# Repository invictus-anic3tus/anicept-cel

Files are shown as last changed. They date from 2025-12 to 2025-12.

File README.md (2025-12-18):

<div align="center">
  Anicept Cel Title Image

  <h2>By Anicetus</h2>

  <p display="inline">
  
  <a href="https://creativecommons.org/licenses/by-nc/4.0/">
    </a> <a href="https://hackclub.com/highway">
    
  </a>

  </p>

  <h4>A tiny yet mighty, sturdy and swift 3D printer, designed and optimized to run at tremendous speeds.</h4>
</div>

<sub>This work is licensed under a
[Creative Commons Attribution-NonCommercial 4.0 International License](https://creativecommons.org/licenses/by-nc/4.0/).
</sub>

## Table of Contents

- [About](#about)
- [Features and Specifications](#features-and-specifications)
- [Assembly](#assembly)
- [Bill of Materials](#bill-of-materials)
- [Contributing](#contributing)

# About

Well, here we go again. My name is Anicetus, and this is my second 3D printer design to date. The first flopped miserably, due to numerous issues in the design phase that either I overlooked or missed due to a lack of research.

Not this time.

This time, I'm making a _real_ printer. Not just another mid ender 3 clone, this is (or should be; as I'm writing this I haven't built it lol) something special. But let's start with the name, shall we? It's called the Anicept Cel. The first part is easy enough to explain--any dedicated hardware enthusiast should have a brand name. Anicept is a combination of Anicetus and concept, and I like how it feels. As for Cel, it's my newfound custom to name my printers with three-letter words. I took Cel from the Latin word celer, or "fast". Maybe that tells you a bit about what I was going for here.

That's right, this printer is made for speed. Everything about it, from the head to the feet (ha) was specifically bent on pure speed. Of course, I'm not an infinite money generator, so I had limits. But not _that_ many limits.

# Features and Specifications

- 180 x 180 x 160 mm print size, plenty for almost all applications
- 300°C max printing temp
- Uses the Peopoly Lancer Long Melt Zone hotend, capable of up to 60mm<sup>3</sup>/s flow rate
- Powerful sheet cooling, best for PETG and ABS/ASA, with the use of two 5020 part cooling fans
- Uses the CR-Touch, one of the most precise (and expensive lol) ABL probes available
- All-4040 extrusion frame, increasing sturdiness exponentially
- MGN12H rails all-around, minimizing wobble
- AWD (all wheel drive) on both Y and X axes, exponentially increasing its power
- Belted Z axis
- Separate electronics enclosure, for ease of use/assembly and to allow enclosing the main printer
- Extra 48V PSU for motors only, increasing their torque
- 9mm belt on X and Y axes
- Uses the powerful Octopus Pro mainboard, equipped with TMC5160T Pros for the X and Y axes
- Uses the Protoextruder, an open-source, DIY filament extruder
- Compatible with the Pico MMU and filament cutter, enabling 4-color and multimaterial printing

# Assembly

coming soon...

# Bill of Materials

Very WIP!! Also this is my personal BOM, like what I own and don't own. Aliexpress prices subject to change _violently_.

|Item |Link |Alt link |Cost |Quantity|Extended Cost|Notes |
|---|---|---|---|---|---|---|
|Electronics |$172.85 | | | | | |
|24V 600W PSU |https://www.digikey.com/en/products/detail/mean-well-usa-inc/LRS-600-24/16394242 | |$70.00 |1 |$0.00 |Owned |
|48V 480W PSU |https://www.amazon.com/REALSUN-Universal-Switching-Converter-Transformer/dp/B096VJMQFM/| |$26.99 |1 |$26.99 | |
|BigTreeTech Octopus Pro + TMC5160T Pro x 4|https://www.aliexpress.us/item/3256803375036597.html | |$100.26|1 |$100.26 | |
|TMC2209 |https://www.aliexpress.us/item/3256805074646808.html | |$0.99  |4 |$3.96 | |
|24v 4010 Axial Fan |https://www.aliexpress.us/item/3256803185681643.html | |$0.99  |1 |$0.99 |(2 pcs needed, 1 owned) |
|RPi 4B 1GB RAM |https://www.ebay.com/itm/167900769294 | |$24.99 |1 |$24.99 | |
|Power inlet |https://www.aliexpress.us/item/3256806175041706.html | |$1.53  |1 |$0.00 |Owned |
|Power cord |https://www.aliexpress.us/item/3256802936747637.html | |$2.61  |1 |$0.00 |Owned |
|On button |https://www.adafruit.com/product/481 | |$4.95  |1 |$0.00 |Owned |
|Heated bed |https://www.aliexpress.us/item/3256807101964868.html | |$14.67 |1 |$14.67 |2M cable? |
|1M 13mm Wire sleeve |https://www.aliexpress.us/item/3256802043851957.html | |$0.99  |1 |$0.99 | |
|Zip ties | | |$2.00  |1 |$0.00 |Owned |
|12AWG Wire |https://www.aliexpress.us/item/3256806250298216.html | |$0.99  |1 |$0.99 |2 M - 1m red, 1m black |
|12AWG Fork Connectors (18 min) |https://www.aliexpress.us/item/3256805357612913.html | |$0.99  |1 |$0.99 |8mm outer width, >= 4mm ID |
|12AWG Female Fork Connectors | | |$0.99  |3 |$0.00 |Owned |
|Frame |$91.47 | | | | | |
|4040 x 600mm extrusion (4 pack) |https://www.amazon.com/gp/product/B09MYL6XMY/ | |$62.99 |1 |$62.99 |Self-cut |
|2020 x 250mm extrusion |https://www.aliexpress.us/item/3256803124984194.html |https://www.aliexpress.us/item/3256804493383834.html|$7.10  |1 |$7.10 | |
|T Plates |https://www.aliexpress.us/item/3256806516993865.html |https://www.aliexpress.us/item/3256806574844240.html|$7.91  |1 |$7.91 | |
|Bed plate |https://www.aliexpress.us/item/3256802956143480.html | |$12.48 |1 |$12.48 | |
|M5 Tap |https://www.aliexpress.us/item/3256805979008585.html | |$0.99  |1 |$0.99 | |
|Tap Wrench |https://www.aliexpress.us/item/3256808061844390.html | |$0.99  |1 |$0.99 | |
|Motion |$41.74 | | | | | |
|X/Y Motors |https://www.aliexpress.us/item/2255801033887365.html | |$22.55 |1 |$0.00 |Owned |
|MGN12H x 250 |https://www.aliexpress.us/item/2255800576028509.html | |$9.05  |3 |$27.15 |(owned: 2, total qty: 5) |
|9mm 2GT Belt |https://www.aliexpress.us/item/3256806321466333.html | |$13.35 |1 |$0.00 |Owned |
|16T 10W 5B Pulley (5 pcs) |https://www.aliexpress.us/item/2251832595367020.html | |$0.99  |1 |$0.99 | |
|20T 10W 5B Pulley | | | |2 |$0.00 |Y axis, owned |
|605 (5x14x5) Bearing (10pcs) |https://www.aliexpress.us/item/3256807482131308.html | |$0.99  |1 |$0.99 |4 Owned, 10 to buy |
|Z axis | | | | | | |
|Motors |https://www.aliexpress.us/item/3256808273084374.html | |$2.46  |2 |$4.92 | |
|80T - 20T pulley, 200mm belt reduction kit|https://www.aliexpress.us/item/3256808844764521.html | |$1.37  |2 |$2.74 | |
|20T 6W 5B Pulley |https://www.aliexpress.us/item/3256806031359840.html | |$0.99  |1 |$0.99 |(owned: 1, total qty: 2) |
|20T 6W 5B Idler |https://www.aliexpress.us/item/2251832631013486.html | |$0.99  |2 |$1.98 | |
|6mm 2GT belt (2M) |https://www.aliexpress.us/item/3256806321466333.html | |$0.99  |1 |$0.99 | |
|M5x45 Dowel pin |https://www.aliexpress.us/item/3256806837028480.html | |$0.99  |1 |$0.99 |(6 pcs min, self cut) |
|Printhead |$85.45 | | | | | |
|Orbiter V2.0/V2.5 |https://www.aliexpress.us/item/3256807258760130.html | |$34.28 |1 |$0.00 |Owned |
|Peopoly Lancer Long Melt Zone |https://peopoly.net/products/magneto-x-lancer-melt-zone | |$58.00 |1 |$58.00 | |
|5020 Fan (2pcs) |https://www.aliexpress.us/item/3256807407728580.html | |$9.53  |1 |$9.53 | |
|CR Touch |https://www.aliexpress.us/item/3256806043295649.html | |$14.95 |1 |$14.95 | |
|Microswitch (3pcs; 2pcs used for X+Y axes)|https://www.aliexpress.us/item/3256804568049753.html | |$0.99  |1 |$0.99 | |
|ADXL345 |https://www.aliexpress.us/item/3256806996565152.html | |$2.33  |1 |$0.00 |Owned |
|3010 Heat Sink Cooling Fan |https://www.aliexpress.us/item/3256803185681643.html | |$0.99  |1 |$0.00 |Owned |
|Filament Cutter + Sensor | | | | | | |
|4mm OD 2mm ID PTFE Tube |https://www.aliexpress.us/item/3256806056618135.html | |$2.01  |1 |$0.00 |Owned |
|Exacto Knife #11 Blade |https://www.aliexpress.us/item/3256808331067380.html | |$0.99  |1 |$0.99 | |
|4mm Ball Bearing |https://www.aliexpress.us/item/3256803905354831.html | |$0.99  |1 |$0.99 | |
|Fasteners and Miscellaneous |$16.10 | | | | |EXACT SCREW NEEDS ARE WIP! |
|Nozzle wiper |https://www.aliexpress.us/item/3256807315758369.html | |$0.99  |1 |$0.99 | |
|M3x22 SHCS | | | |4 |$0.00 |Owned |
|M3x30 SHCS | | | |4 |$0.00 |Owned |
|M3x8 SHCS | | | |7 |$0.00 |Owned |
|M3x6 SHCS | | |$0.99  |1 |$0.99 |for the electronics box |
|M3x14 SHCS | | | |12 |$0.00 |Owned |
|M4x12 FHCS | | | |6 |$0.00 |for the bed & X axis tensioner (owned)|
|M5x50 SHCS |https://www.aliexpress.us/item/2255800598515019.html | | |40 |$3.96 | |
|M5x14 SHCS |https://www.aliexpress.us/item/2255800598515019.html | | |10 |$0.99 |(Total 22, owned 12) |
|2020 M3 T Nuts (50 pcs) |https://www.aliexpress.us/item/3256807638725964.html | | |1 |$0.99 | |
|2020 M5 T Nuts (50 pcs) |https://www.aliexpress.us/item/2251832778465720.html | | |1 |$0.99 | |
|M5 Two-Stage Drill Bit |https://www.aliexpress.us/item/3256805825438819.html | |$6.20  |1 |$6.20 | |
|M3x4mm 5mm OD inserts |https://www.aliexpress.us/item/3256803396040989.html | |$0.99  |1 |$0.99 | |
|M4x8mm 6mm OD inserts | | | | |$0.00 |Owned |
|M5x8mm 7mm OD inserts |https://www.aliexpress.us/item/3256803396040989.html | |$0.99  |1 |$0.99 | |
|Total | | | | |$411.57 | |
|Tax | | | | |$33.95 | |
|Grand Total | | | | |$445.52 | |

# Contributing

If you'd like to request something, give feedback, or wish to make your own changes, simply open an issue on this repository or email me! (My email is in my profile.)



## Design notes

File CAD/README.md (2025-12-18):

Hi there! Herein lies the complete (WIP!) files for the Anicept Cel and its electronics box. In the 3D_Print directory, you'll find all the files you need to 3D print, categorized as seen fit.













thats it. go away

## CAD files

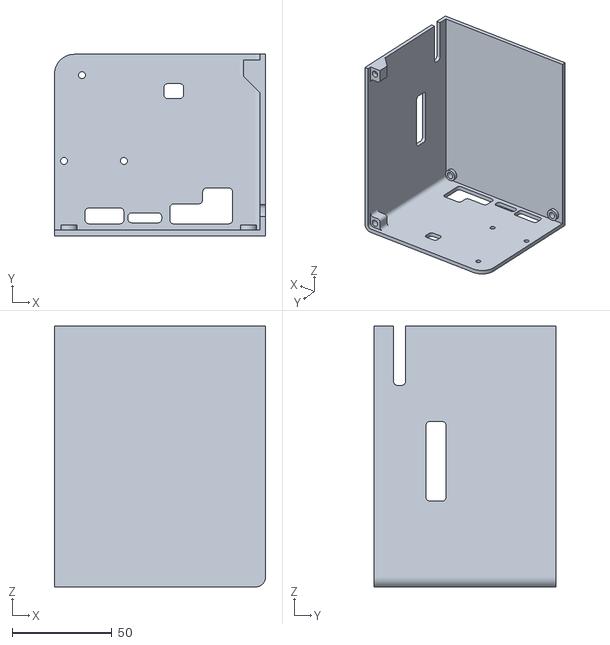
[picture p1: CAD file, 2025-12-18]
CAD/3D_Print/Electronics_Box/Main Casing 2.stl
105.8 x 91.0 x 130.8

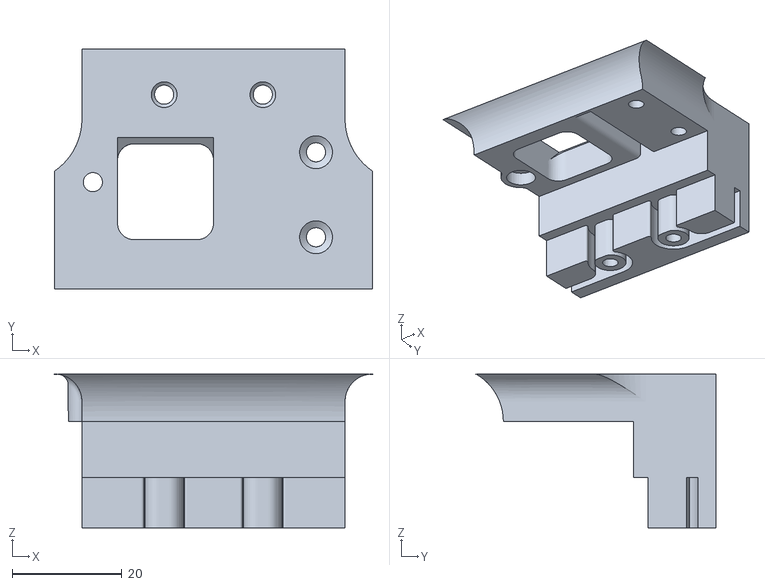
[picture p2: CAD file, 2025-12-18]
CAD/3D_Print/Main_Printer/Printhead/Printhead Back Main.stl
58.0 x 43.8 x 28.1

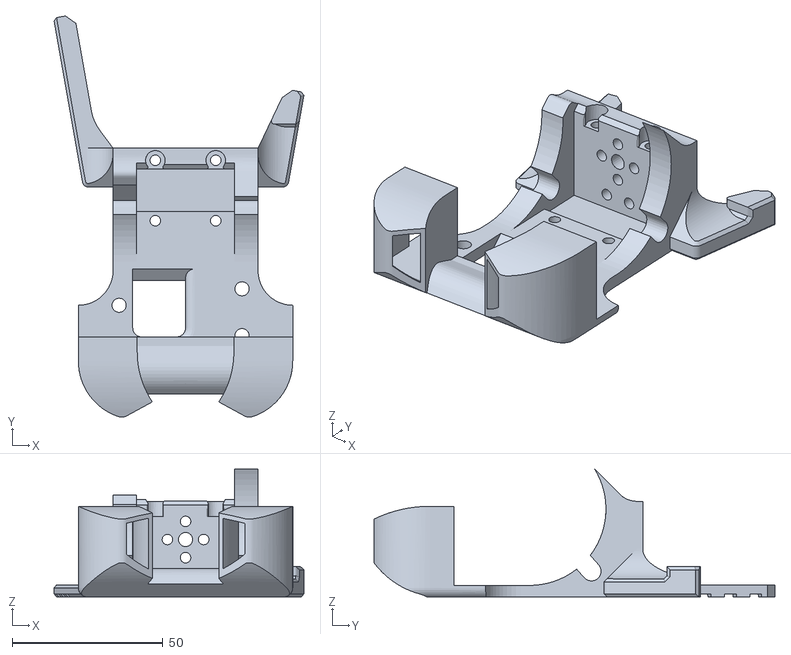
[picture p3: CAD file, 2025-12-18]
CAD/3D_Print/Main_Printer/Printhead/Printhead Main.stl
82.7 x 132.8 x 42.4

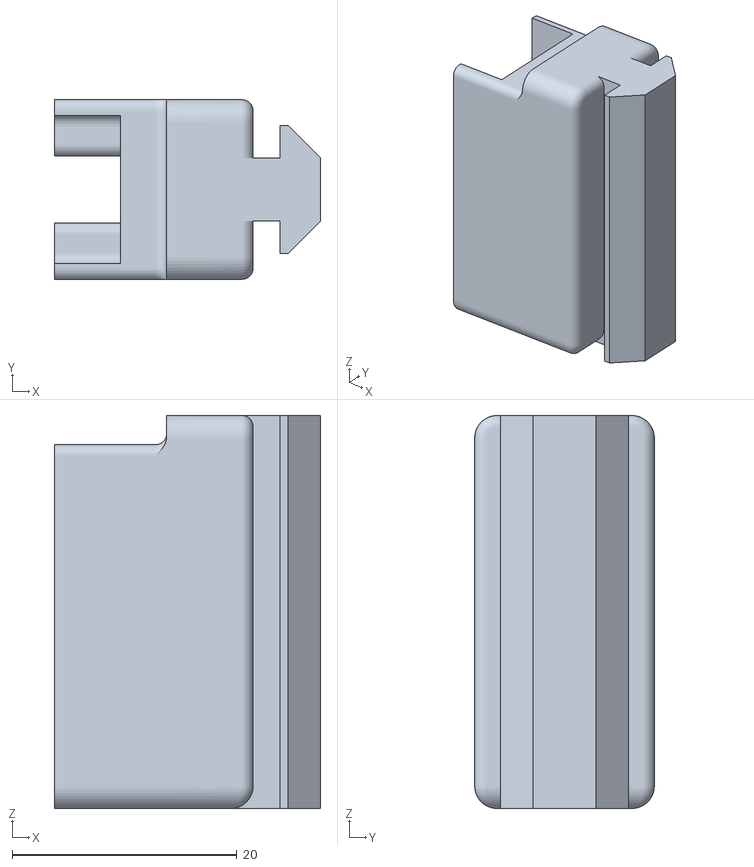
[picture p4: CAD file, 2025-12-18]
CAD/3D_Print/Main_Printer/Y_Axis/Y Axis Endstop Main.stl
23.7 x 16.0 x 35.0

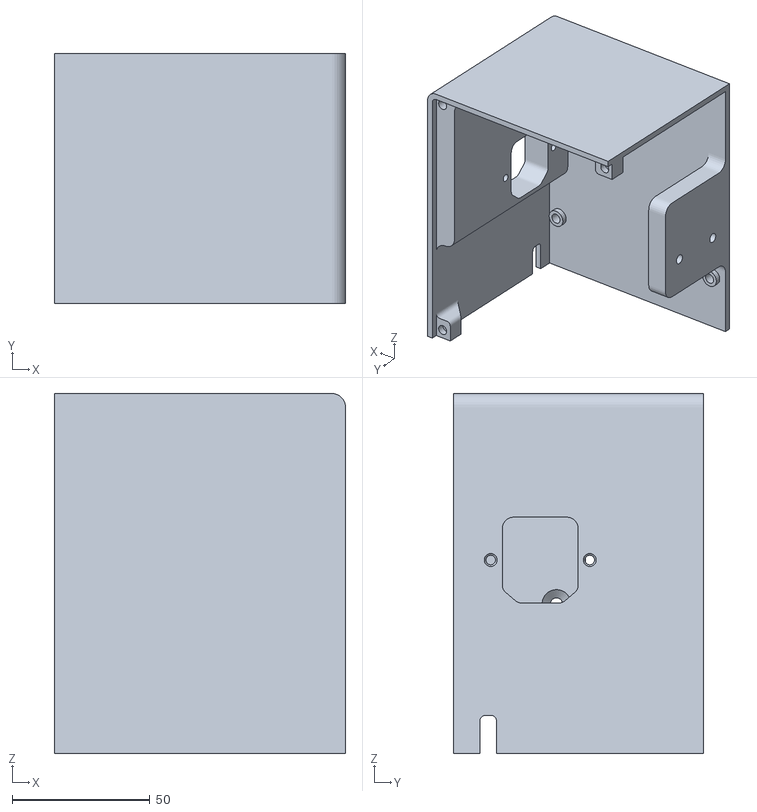
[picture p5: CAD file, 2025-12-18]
CAD/3D_Print/Electronics_Box/Main Casing 1.stl
105.8 x 91.0 x 130.8

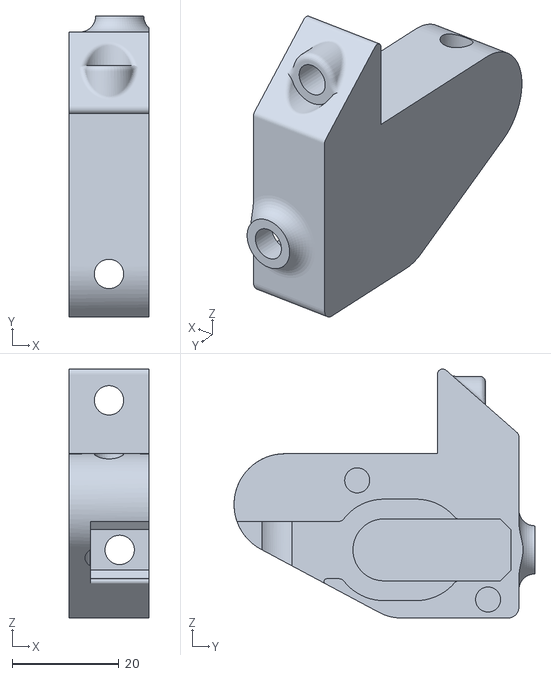
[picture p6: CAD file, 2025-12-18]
CAD/3D_Print/Main_Printer/Z_Axis/Z Axis Left Belt Tensioner Main.stl
15.0 x 56.3 x 46.6

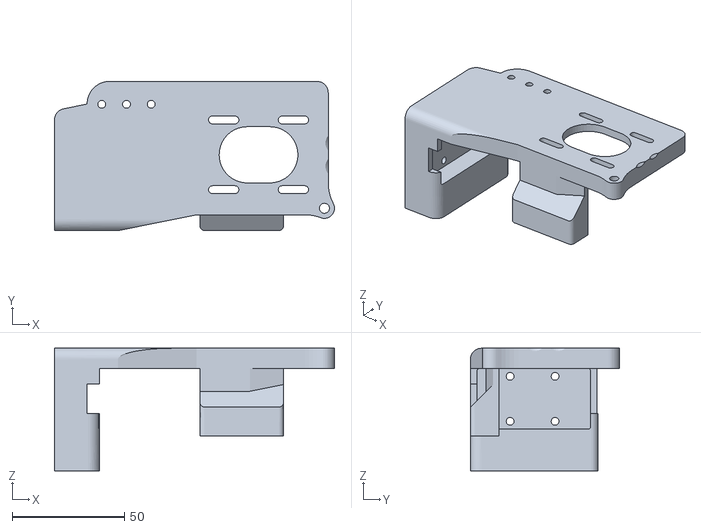
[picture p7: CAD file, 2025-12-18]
CAD/3D_Print/Main_Printer/X_Axis/X Axis Right Motor Mount.stl
124.5 x 66.4 x 54.5

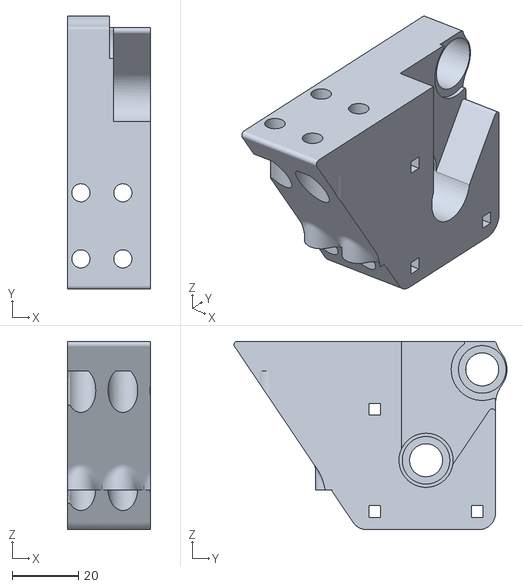
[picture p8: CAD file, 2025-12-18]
CAD/3D_Print/Main_Printer/Y_Axis/Back/Back Y Axis Cover.stl
25.2 x 82.6 x 57.0

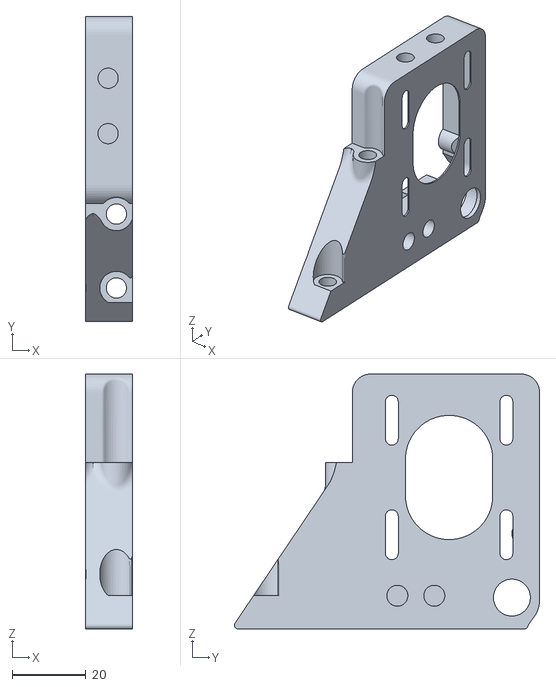
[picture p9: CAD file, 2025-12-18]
CAD/3D_Print/Main_Printer/Y_Axis/Front/Front Y Axis Tensioner Motor Mount.stl
12.6 x 82.6 x 69.0

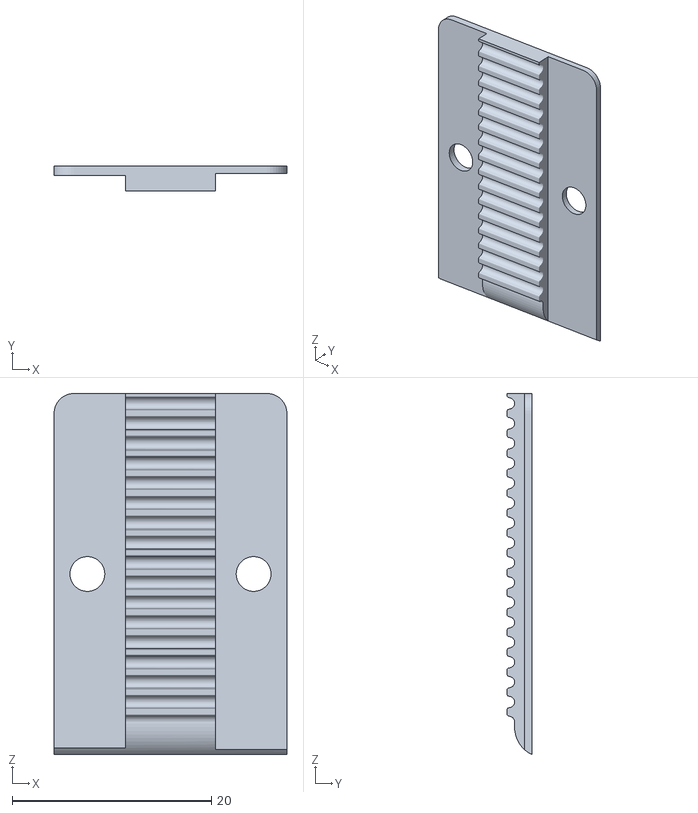
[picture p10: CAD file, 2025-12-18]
CAD/3D_Print/Main_Printer/Y_Axis/Y Axis Front Belt Clamp.stl
23.4 x 2.47 x 36.3

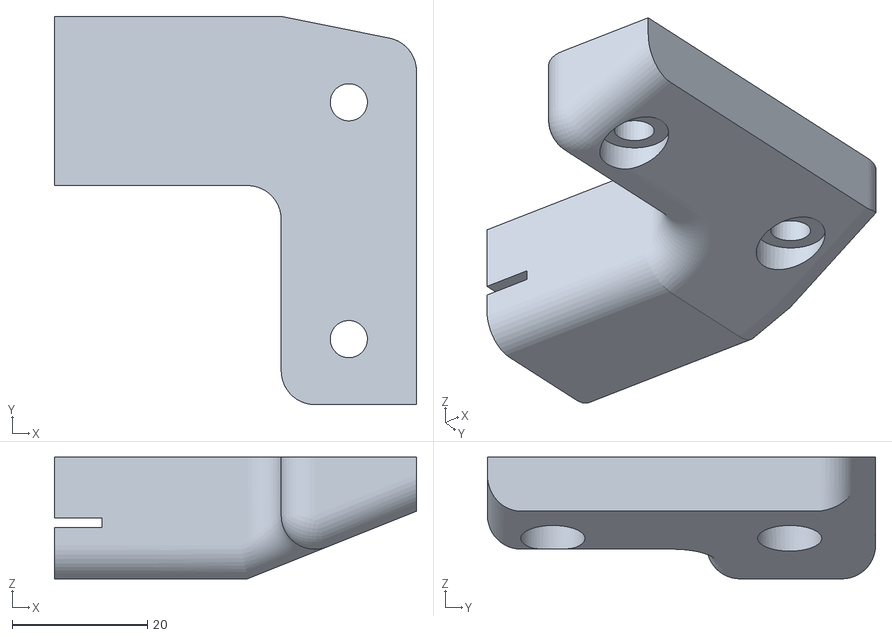
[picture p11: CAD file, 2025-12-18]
CAD/3D_Print/Main_Printer/Z_Axis/Z Axis Left Belt Clamp.stl
53.5 x 57.4 x 18.0

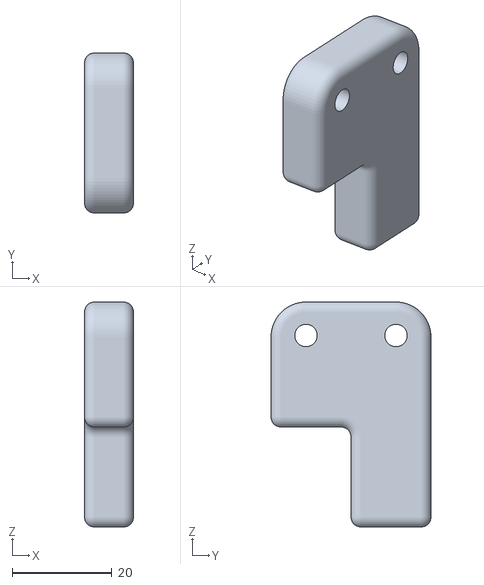
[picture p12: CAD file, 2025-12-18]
CAD/3D_Print/Electronics_Box/Large Connector.stl
9.80 x 32.0 x 45.0

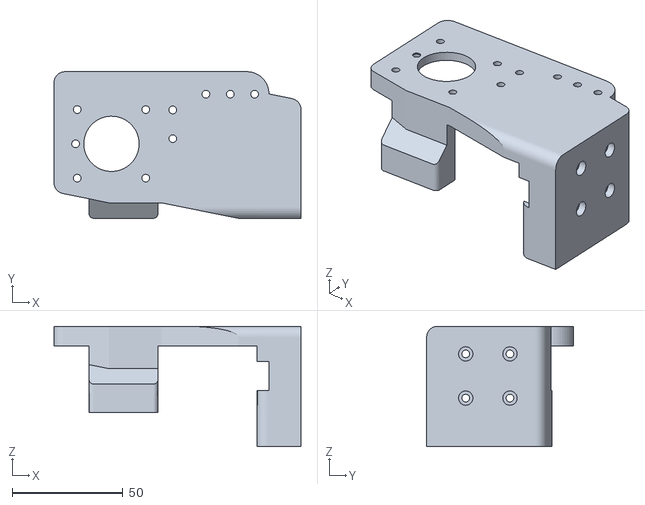
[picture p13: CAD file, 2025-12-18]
CAD/3D_Print/Main_Printer/X_Axis/X Axis Left Motor Mount.stl
111.7 x 66.4 x 54.5

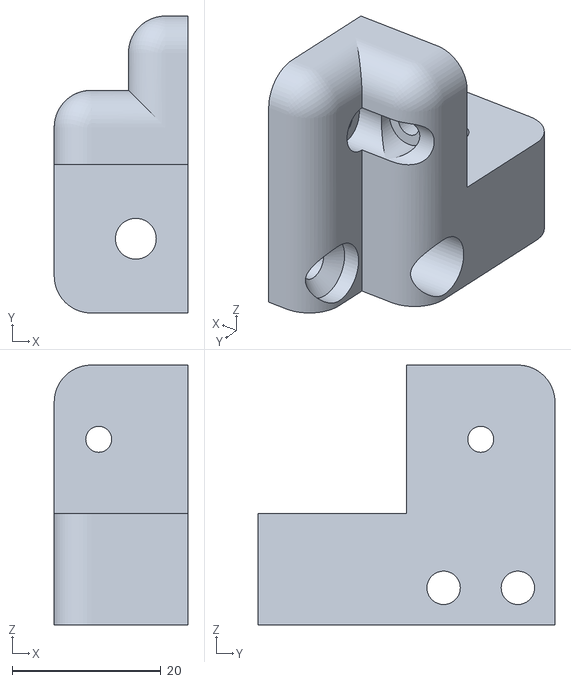
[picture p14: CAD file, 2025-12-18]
CAD/3D_Print/Main_Printer/Y_Axis/Back/Back Y Axis Right Extrusion Connector.stl
18.0 x 40.0 x 35.0

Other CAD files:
CAD/3D_Print/Main_Printer/Z_Axis/Z Axis Right Belt Tensioner Main.stl
CAD/3D_Print/Main_Printer/Y_Axis/Front/Front Y Axis Tensioner Moving Block Bottom.stl
CAD/3D_Print/Main_Printer/Y_Axis/Y Axis Bed Chassis.stl
CAD/3D_Print/Main_Printer/Z_Axis/Z Axis Left Belt Tensioner Block.stl
CAD/3D_Print/Electronics_Box/Back PSU Cover.stl
CAD/3D_Print/Electronics_Box/Fan Mount.stl
CAD/3D_Print/Electronics_Box/Front PSU Cover.stl
CAD/3D_Print/Electronics_Box/Side Panel.stl
CAD/3D_Print/Electronics_Box/Small Connector.stl
CAD/3D_Print/Electronics_Box/Top Panel 1.stl
CAD/3D_Print/Electronics_Box/Top Panel 2.stl
CAD/3D_Print/Main_Printer/Printhead/Printhead Back Panel.stl
CAD/3D_Print/Main_Printer/Printhead/Printhead Inner Mount.stl
CAD/3D_Print/Main_Printer/X_Axis/Filament Cutter Trigger.stl
CAD/3D_Print/Main_Printer/X_Axis/X Axis Left Motor Cover.stl
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

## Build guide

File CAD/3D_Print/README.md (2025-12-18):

If possible, all parts on the main printer should be printed in ABS, ASA, or PETG. If you have to, the Z axis components can be printed in PLA, and so can the printhead. The electronics box can be printed in whatever you please.

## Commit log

2025-12-18 Add BOM file
    [BOM.csv]
2025-12-18 Create README.md for CAD folder
2025-12-18 Add front Y axis print files
    [Front Y Axis Left Extrusion Connector.stl, Front Y Axis Right Extrusion Connector.stl, Front Y Axis Tensioner Cover.stl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]
2025-12-18 Create Y_Axis/Back
2025-12-18 Upload all print files
    All the files to 3D print the anicept cel
    [Back PSU Cover.stl, Fan Mount.stl, Filament Cutter Trigger.stl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]
